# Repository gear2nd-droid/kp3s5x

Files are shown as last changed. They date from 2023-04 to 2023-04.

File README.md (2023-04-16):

# kp3s5x
Adding 2 axes to the kp3s, a common 3D printer, to convert it into a 5-axis 3D printer.



youtube (https://www.youtube.com/watch?v=lcaOiuYi4Ac)

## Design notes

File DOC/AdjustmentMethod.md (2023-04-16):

# BC axis adjustment

## Platform adjustment
Align the plane of the platform and bearing.
1. Place a ruler on the front and back ribs of the B-axis carriage with the edges facing each other.
2. Align the edge of the ruler with the height of the platform.
3. Place the nozzle on the platform, and with the nozzle fixed, adjust the distance between the nozzle and the platform while rotating the C-axis manually.
4. Again, apply the ruler and adjust it so that the edge of the platform and the edge of the ruler are in contact.

## A-axis rotational deflection compensation
The weight of the B-axis motor causes the platform to deflect in the A-axis direction and tilt. This is the correction.
1. Measure the distance between the nozzle and the platform when the nozzle is operated with X=0, Y=Change, Z=Fixed.
2. Adjust "offset_a" in the [printer] section to keep the spacing constant.

# XYZ axis adjustment
The intersection of the rotation axes of the B and C axes must be the XYZ origin.

## Z home position adjustment
1. Adjust the "position_endstop" in the [stepper_z] section so that z=0 on the platform.
2. Deflection compensation results in a larger change than the change in "position_endstop". Please pay attention to this.

## X/Y home position adjustment
1. While dispensing, rotate the C-axis and adjust it so that it becomes a single point instead of a circle.
2. Adjust "position_endstop" in [stepper_x] and [stepper_y] for adjustment parameters.

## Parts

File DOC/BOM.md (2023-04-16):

|Item|Quantity|Description|Link|
|---|---|---|---|
|Bearing C-B688ZZ|2|||
|Bearing RB2508UUC0|1|||
|20T 6mm Pulley (5mm bore)|2|||
|80T 6mm Pulley (5mm bore)|1|||
|80T 6mm Pulley (20mm bore)|1|||
|GT2-closed loop-220mm width 6mm|1|||
|GT2-closed loop-200mm width 6mm|1|||
|Photo sensor|2||https://ja.aliexpress.com/item/32791528678.html|
|NEMA17 20mm size|1||https://ja.aliexpress.com/item/1005003226027617.html|
|NEMA17 normal size|1||
|Cap screw M3x15|8|||
|Cap screw M3x10|8|||
|Cap screw M3x8|16|||
|Cap screw M3x5|14|||
|Washer M3|34|||
|Nut M3|16|||
|Heatset M3x4|39|M3xD4.2xL4.0||

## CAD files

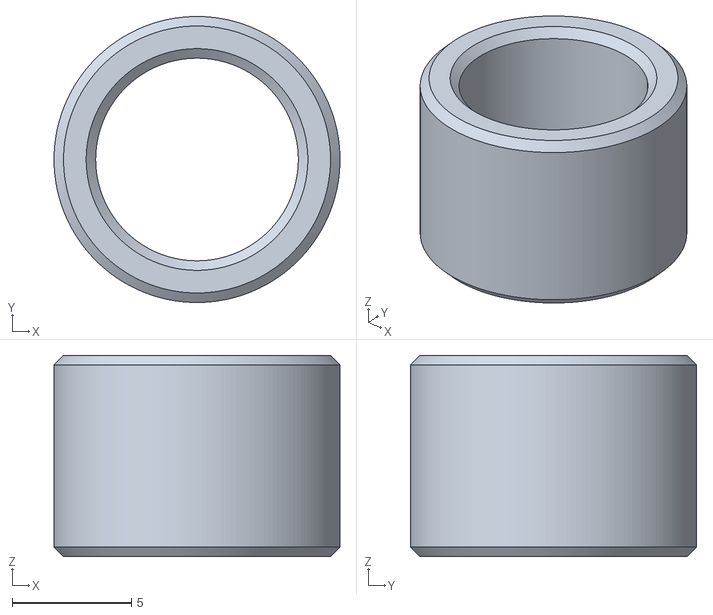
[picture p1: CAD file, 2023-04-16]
STL/Spacer2.stl
12.0 x 12.0 x 8.45

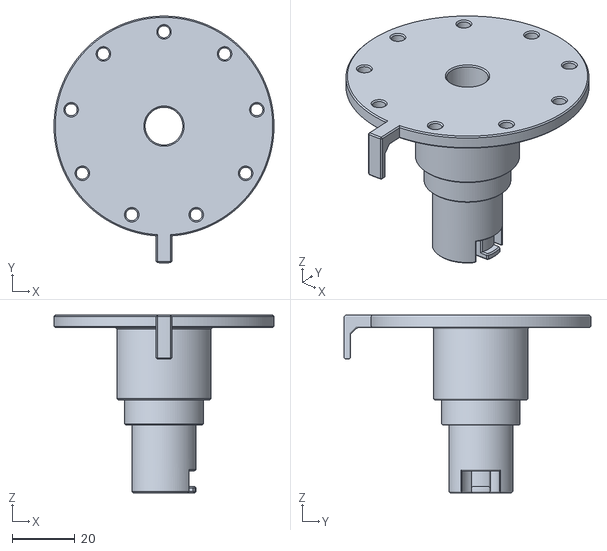
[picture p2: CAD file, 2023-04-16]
STL/C_Carriage.stl
70.0 x 78.5 x 56.5

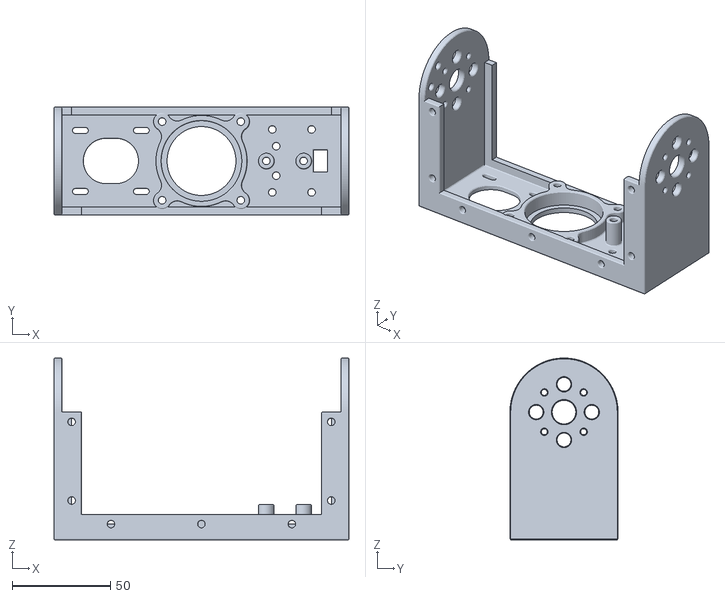
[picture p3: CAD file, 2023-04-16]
STL/B-Carriage.stl
150.0 x 55.0 x 92.5

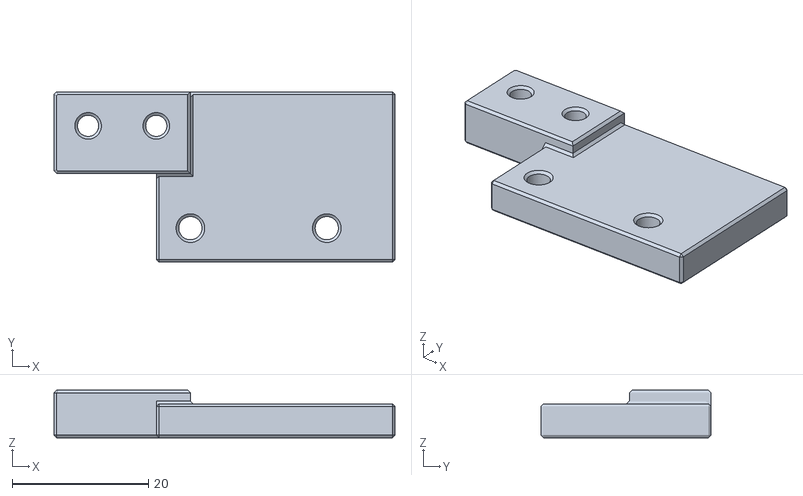
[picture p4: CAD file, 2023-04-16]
STL/ZEndstop.stl
50.0 x 25.0 x 7.00

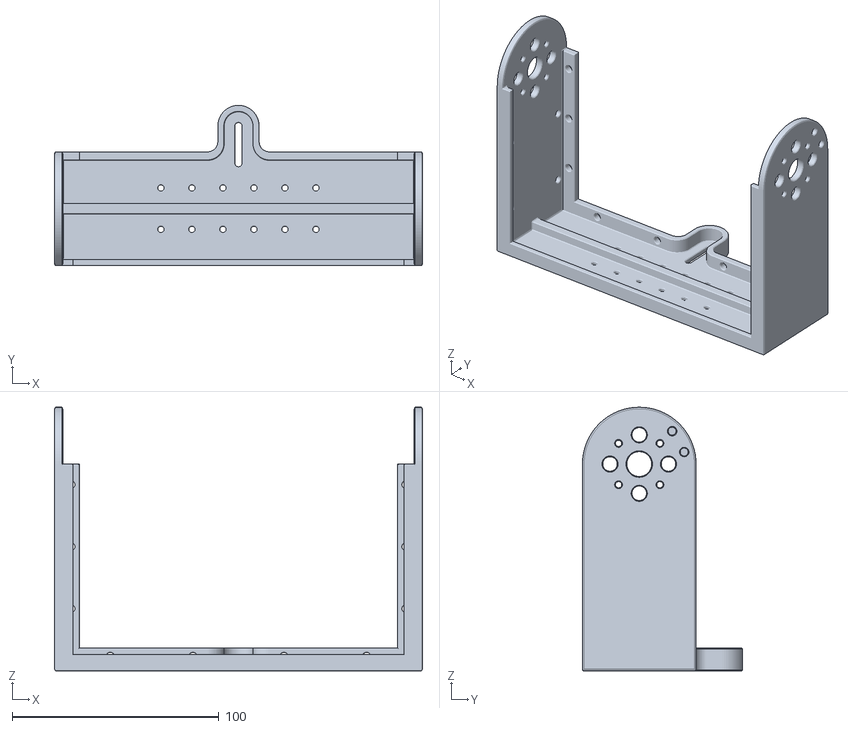
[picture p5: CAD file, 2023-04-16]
STL/Y-Carriage.stl
178.0 x 77.5 x 127.5

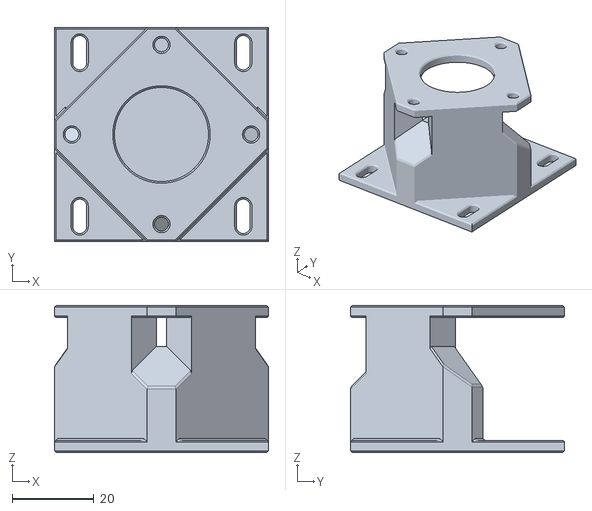
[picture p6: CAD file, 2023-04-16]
STL/Y_Bracket.stl
52.3 x 52.3 x 36.0

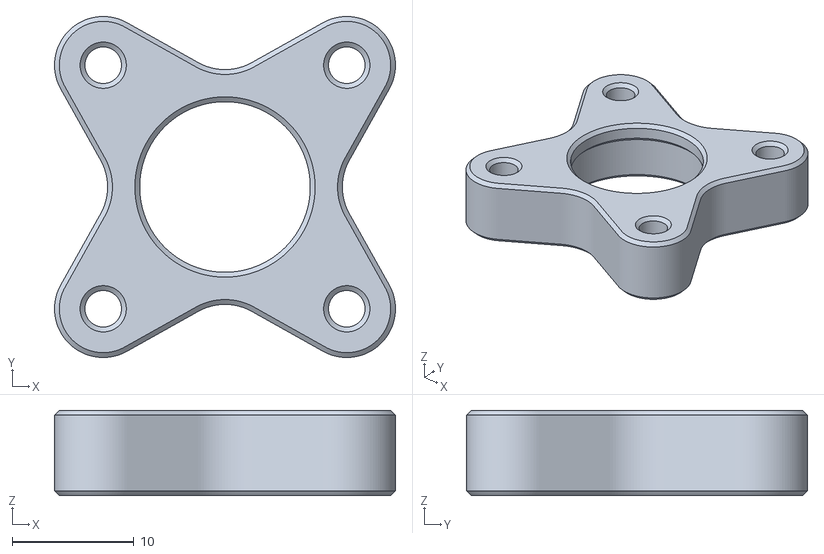
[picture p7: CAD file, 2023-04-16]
STL/BearingHolder.stl
28.0 x 28.0 x 7.00

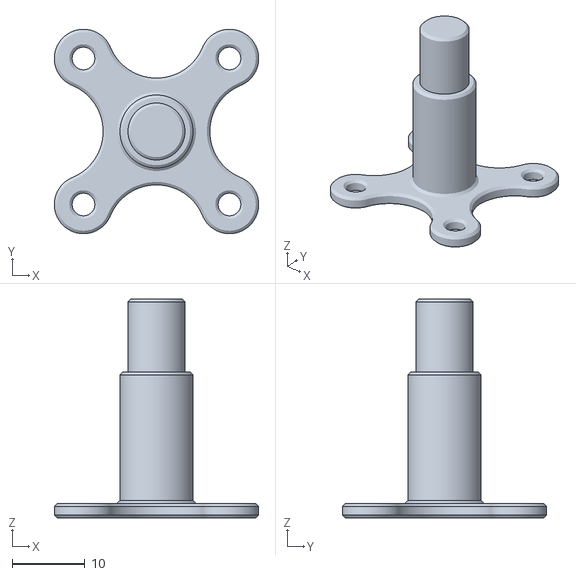
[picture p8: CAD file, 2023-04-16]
STL/B-shaft_1.stl
28.0 x 28.0 x 30.0

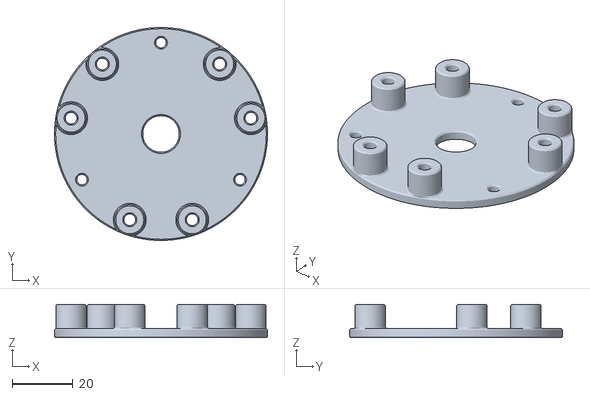
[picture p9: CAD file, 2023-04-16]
STL/circuit_base.stl
70.0 x 70.0 x 11.0

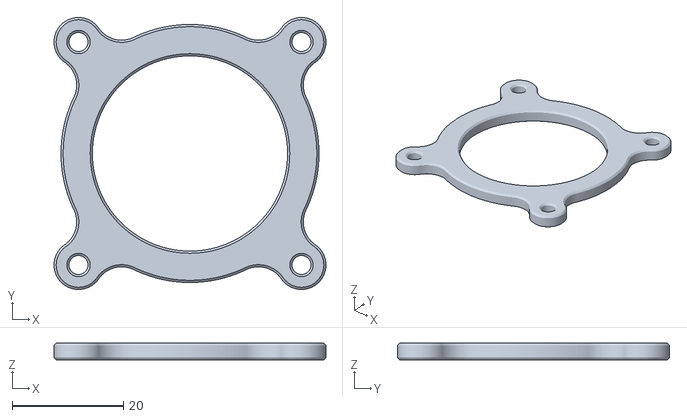
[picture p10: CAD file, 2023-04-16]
STL/Cap.stl
48.8 x 48.8 x 3.00

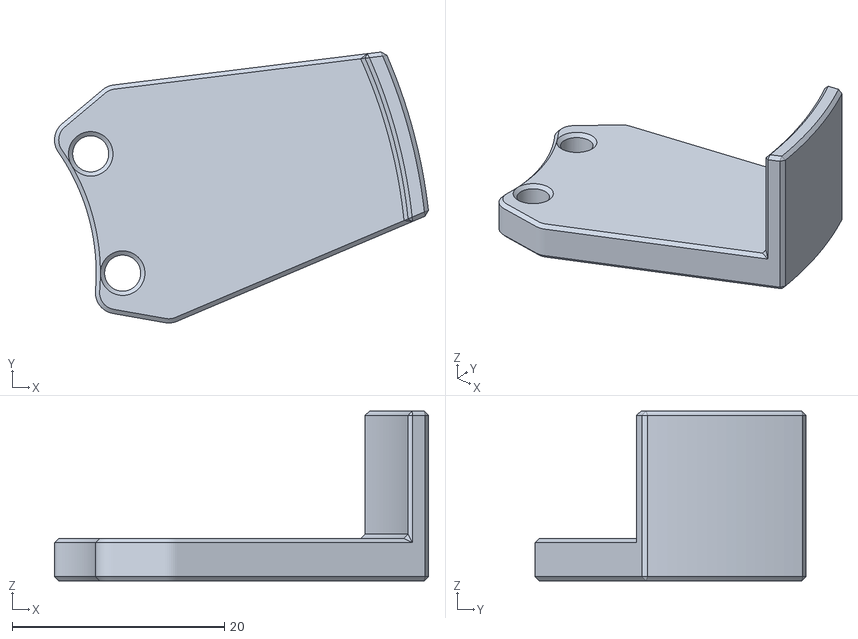
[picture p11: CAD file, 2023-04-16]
STL/BDog.stl
35.3 x 25.6 x 16.0

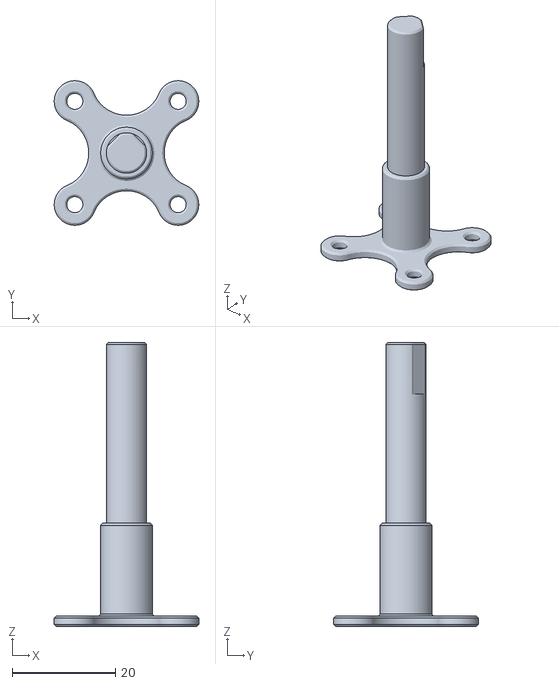
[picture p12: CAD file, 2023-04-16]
STL/B-shaft_2.stl
28.0 x 28.0 x 55.0

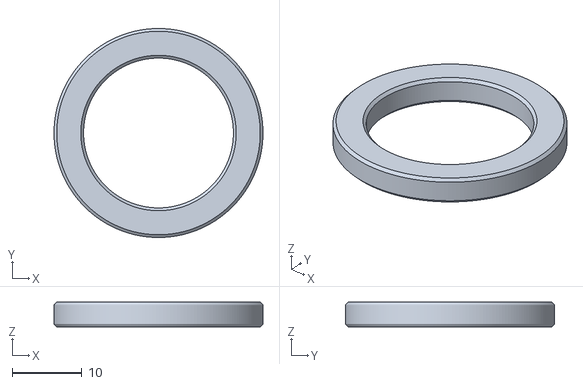
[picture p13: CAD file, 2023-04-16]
STL/Spacer.stl
30.0 x 30.0 x 3.55

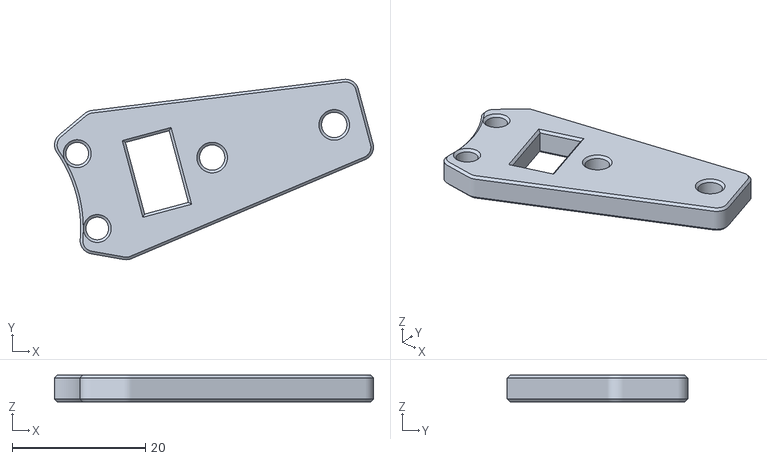
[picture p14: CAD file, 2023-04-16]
STL/BEndstop.stl
48.0 x 27.1 x 4.00

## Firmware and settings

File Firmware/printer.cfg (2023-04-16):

# This file contains common pin mappings for MKS Robin Nano (v1.2.004)
# boards. To use this config, the firmware should be compiled for the
# STM32F103. When running "make menuconfig", enable "extra low-level
# configuration setup", select the 28KiB bootloader, disable "USB for
# communication", and select USART3 for the "Serial Port".

# Note that the "make flash" command does not work with MKS Robin
# boards. After running "make", run the following command:
#   ./scripts/update_mks_robin.py out/klipper.bin out/Robin_nano.bin
# Copy the file out/Robin_nano.bin to an SD card and then restart the
# printer with that SD card.

# See the example.cfg file for a description of available parameters.

[printer]
kinematics: trunnion_bc
max_velocity: 300
max_accel: 500
max_accel_to_decel: 500
max_z_velocity: 25
max_z_accel: 100
square_corner_velocity: 5.0
is_6axes: True
after_homing_z_position: 20
before_homing_z_move_x: 40
before_homing_z_move_y: 0
offset_x: 0.0
offset_y: 0.0
offset_z: 0.0
offset_a: -3.5#-1.1
offset_b: 0.0
offset_c: 0.0

[input_shaper]
shaper_freq_x: 41.4
shaper_freq_y: 29.2
shaper_type: mzv

[extruder]
step_pin: PD6
dir_pin: !PD3
enable_pin: !PB3
# for MK8 Extruder
rotation_distance: 7.64
full_steps_per_rotation: 200
microsteps: 32
max_extrude_only_distance: 100000
nozzle_diameter: 0.400
filament_diameter: 1.750
max_extrude_only_velocity: 50
max_extrude_only_accel: 3000
instantaneous_corner_velocity: 1.50
heater_pin: PC3
sensor_type: EPCOS 100K B57560G104F
sensor_pin: PC1
control: pid
pid_Kp: 19.040
pid_Ki: 1.076
pid_Kd: 84.251
min_temp: 0
max_temp: 280
pressure_advance: 0.08

#[virtual_sdcard]
#path: ~/gcode_files
[virtual_sdcard]
path: /home/pi/printer_data/gcodes

[stepper_x]
step_pin: PE3
dir_pin: PE2
enable_pin: !PE4
rotation_distance: 40
microsteps: 32
endstop_pin: ^!PA15
position_endstop: -54.5
position_min: -55
position_max: 80
homing_speed: 50
homing_retract_dist: 5
homing_positive_dir: False

[stepper_y]
step_pin: PE0
dir_pin: PB9
enable_pin: !PE1
rotation_distance: 40
full_steps_per_rotation: 200
microsteps: 32
endstop_pin: ^!PA12
position_endstop: -96.7
position_min: -100
position_max: 80
homing_speed: 50
homing_retract_dist: 5
homing_positive_dir: False

[stepper_z]
step_pin: PB5
dir_pin: !PB4
enable_pin: !PB8
rotation_distance: 8
full_steps_per_rotation: 200
microsteps: 32
endstop_pin: ^!PA11 #probe:z_virtual_endstop #defines the Z endstop as the BLtouch
position_endstop: 43.5
position_min: -2
position_max: 60
homing_speed: 10
homing_retract_dist: 0.0
homing_positive_dir: True

[stepper_b]
step_pin: pico:gpio10
dir_pin: pico:gpio11
enable_pin: !pico:gpio14
rotation_distance: 180
full_steps_per_rotation: 200
microsteps: 32
endstop_pin: PC4
position_endstop: -5.5
position_min: -180
position_max: 15
homing_speed: 5
homing_retract_dist: 20

[stepper_c]
step_pin: pico:gpio12
dir_pin: !pico:gpio13
enable_pin: !pico:gpio15
rotation_distance: 180
full_steps_per_rotation: 200
microsteps: 32
endstop_pin: ^pico:gpio9
position_endstop: 5.0
position_min: -3600000
position_max: 3600000
homing_speed: 5
homing_retract_dist: 5
homing_positive_dir: True

[bed_mesh]
speed: 150
horizontal_move_z: 6
mesh_min: 5,5
mesh_max: 145,170
algorithm: bicubic
probe_count: 4,4
fade_start: 1
fade_end: 10

[heater_fan my_nozzle_fan]
pin: PB0
heater: extruder
heater_temp: 50.0
fan_speed: 1.0

#[heater_bed]
#heater_pin: pico:gpio0
#sensor_type: EPCOS 100K B57560G104F
#sensor_pin: pico:gpio26
#control: pid
#pid_Kp: 325.10
#pid_Ki: 63.35
#pid_Kd: 417.10
#min_temp: 0
#max_temp: 70

[fan]
pin: PB1

[mcu]
serial: /dev/serial/by-id/usb-1a86_USB_Serial-if00-port0
restart_method: command

[mcu pico]
serial: /dev/serial/by-id/usb-Klipper_rp2040_E6616407E3697C2A-if00
restart_method: command

[mcu rpi]
serial: /tmp/klipper_host_mcu

[bed_screws]
screw1: 24,24
screw2: 168,24
screw3: 168,168
screw4: 24,168

[static_digital_output display_reset]
pins: !PC6, !PD13

[pause_resume]
recover_velocity: 50

[gcode_arcs]
resolution: 0.1

[display_status]
[pause_resume]

[gcode_macro PAUSE]
description: Pause the actual running print
rename_existing: PAUSE_BASE
gcode:
  PAUSE_BASE
  _TOOLHEAD_PARK_PAUSE_CANCEL {rawparams}

[gcode_macro G29]
gcode:
    BED_MESH_CALIBRATE

[gcode_macro RESUME]
description: Resume the actual running print
rename_existing: RESUME_BASE
gcode:
  ##### get user parameters or use default #####
  {% set macro_found = True if printer['gcode_macro _CLIENT_VARIABLE'] is defined else False %}
  {% set client = printer['gcode_macro _CLIENT_VARIABLE'] %}
  {% set velocity = printer.configfile.settings.pause_resume.recover_velocity %}
  {% set use_fw_retract = False if not macro_found
                     else False if client.use_fw_retract is not defined
                     else True  if client.use_fw_retract|lower == 'true' and printer.firmware_retraction is defined
                     else False %} 
  {% set unretract      = 1.0  if not macro_found else client.unretract|default(1.0)|abs %}
  {% set sp_unretract   = 2100 if not macro_found else client.speed_unretract|default(35) * 60 %}
  {% set sp_move        = velocity if not macro_found else client.speed_move|default(velocity) %}
  ##### end of definitions #####
  {% if printer.extruder.can_extrude %}
    {% if use_fw_retract %}
      G11
    {% else %}
      M83
      G1 E{unretract} F{sp_unretract}
      {% if printer.gcode_move.absolute_extrude %} M82 {% endif %}
    {% endif %}
  {% else %}
    {action_respond_info("Extruder not hot enough %s" % use_fw_retract)}
  {% endif %}  
  RESUME_BASE VELOCITY={params.VELOCITY|default(sp_move)} 

[heater_fan my_nozzle_fan]
pin: PB0
heater: extruder
heater_temp: 50.0
fan_speed: 1.0

[gcode_macro CANCEL_PRINT]
rename_existing: BASE_CANCEL_PRINT
gcode:
    M107
    TURN_OFF_HEATERS
    CLEAR_PAUSE
    SDCARD_RESET_FILE
    BASE_CANCEL_PRINT

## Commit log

2023-04-16 Add 1st gen
    Add 1st gen
    [B-Carriage.stl, B-shaft_1.stl, B-shaft_2.stl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]
2023-04-16 Create printer.cfg
    Add printer config
    [printer.cfg]
